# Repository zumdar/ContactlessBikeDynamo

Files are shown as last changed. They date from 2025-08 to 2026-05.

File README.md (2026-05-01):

# Contactless Bicycle Dynamo using Eddy Currents

This is a [certified Open Source](https://certification.oshwa.org/us002771.html) small electrical generator that creates enough current to power a small bicycle light while your wheel is spinning. 

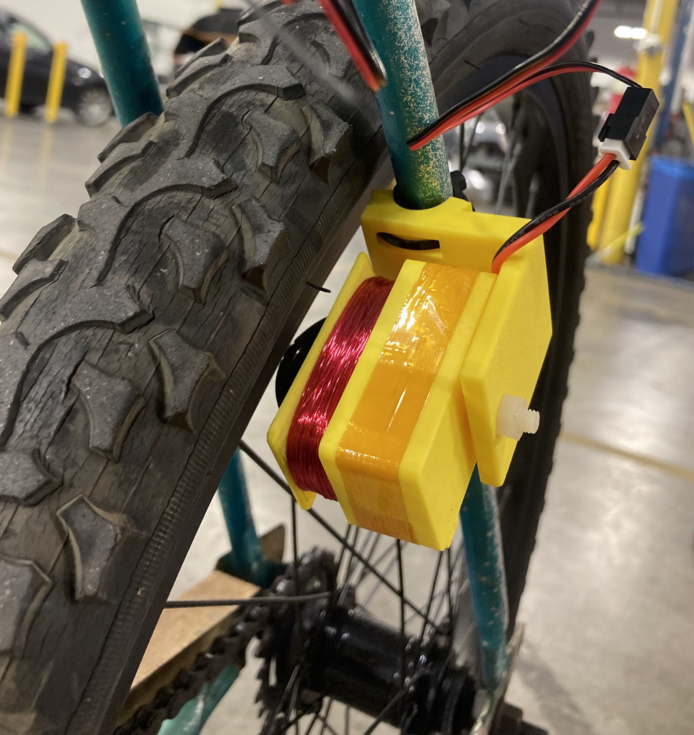
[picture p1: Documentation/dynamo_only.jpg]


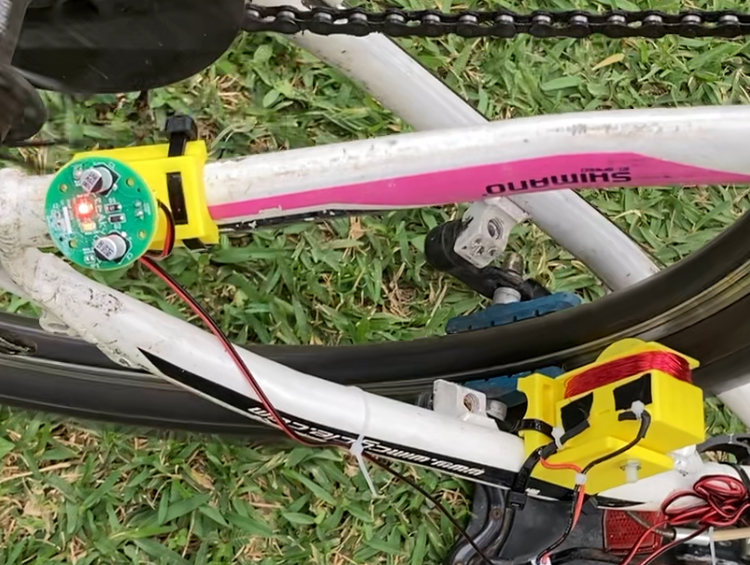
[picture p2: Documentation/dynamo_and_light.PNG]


# Description


The design files here include the physical design files for the Dynamo and the LED light, as well as a custom PCB for the LED light which is a simple voltage rectifier doubler and choice of red or white led. 

If you would like to make this project:
- print off the files in:
  -  \Mechanical\Components\STLs\Final STL
- acquire parts in the Bill of Materials
- aquire tools in the Tool BoM
- follow instructions in the ZINE

This project started off with a desire to be a workshop I could host to show an interesting way to generate electricity and power a bike light without needing a battery. 

Here are the workshop slides:
https://docs.google.com/presentation/d/1txSlyZcSNcTIk4scu_-NPuIz-HN-7od_rSDEqWW2YtM/edit?usp=sharing

# Technical 


## Physical Design Files
The parts are labelled as follows:

- P001-B100	-	Square Dynamo
- P001-B101	-	Dynamo Cover
- P001-B102	-	Magnet Holder Ring
- P001-B103	-	M5 Bearing Adaptor
- P001-B104	-	Fork Bracket
- P001-B105	-	PCB Cover
- P001-B106	-	LED Light Mount

There is also an assembly of the Dynamo labelled:

- P001-B001	-	Dynamo
## PCB Design files

The PCB contains red and white LEDs which can be selected by doing a solder bridge while assembling. 

You can't use both at the same time. If you solder both, only the Red LED will light (it has a lower forward voltage). 

The LED PCB design can be found in:
- \Electrical\Dyno_LED_PCB

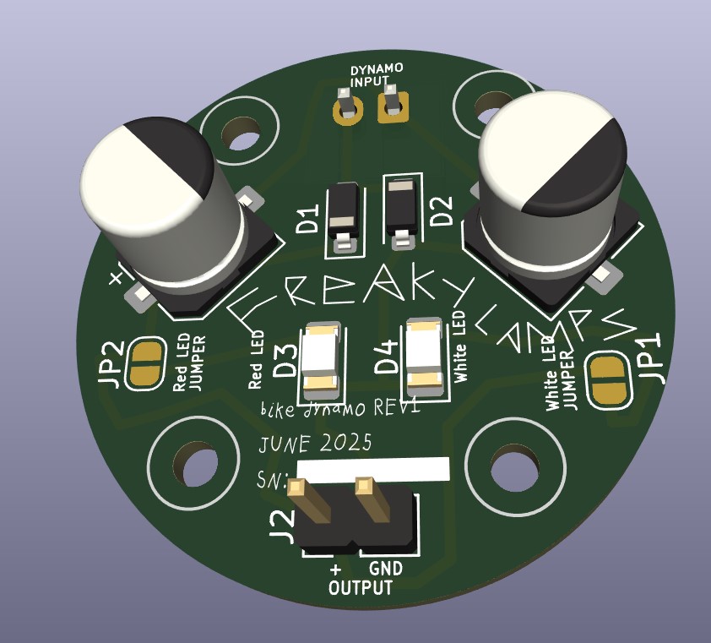
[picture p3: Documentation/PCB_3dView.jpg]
pcb render


# Acknowledgments

Thank you to:
Lucas Ray, Clara Caspard, and YJ Rodrigues for helping develop this! 

# License
This is an certified [open source project](https://certification.oshwa.org/us002771.html)!



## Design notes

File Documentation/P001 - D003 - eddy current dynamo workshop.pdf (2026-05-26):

# free energy

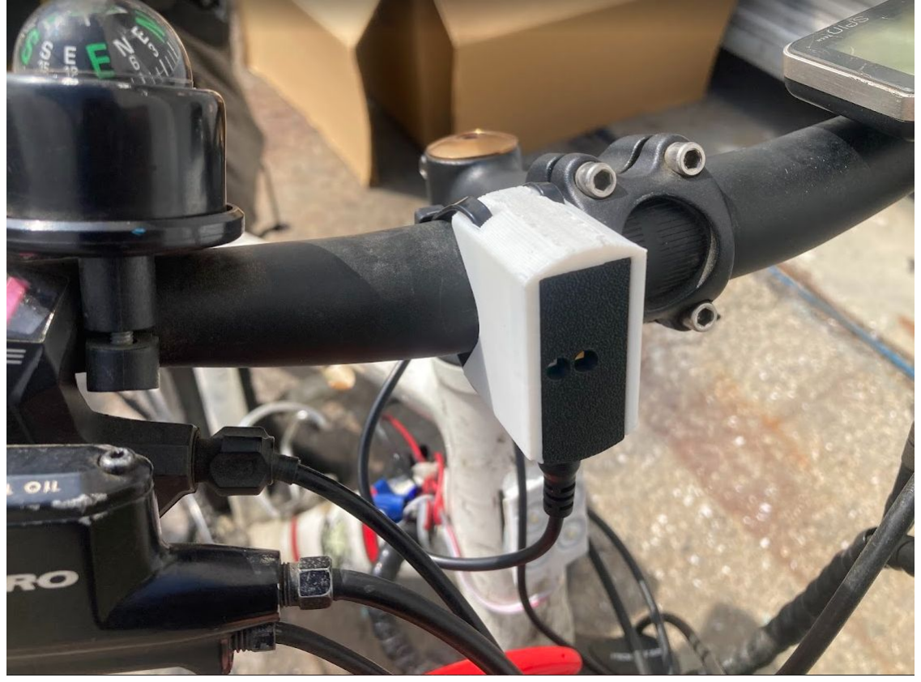
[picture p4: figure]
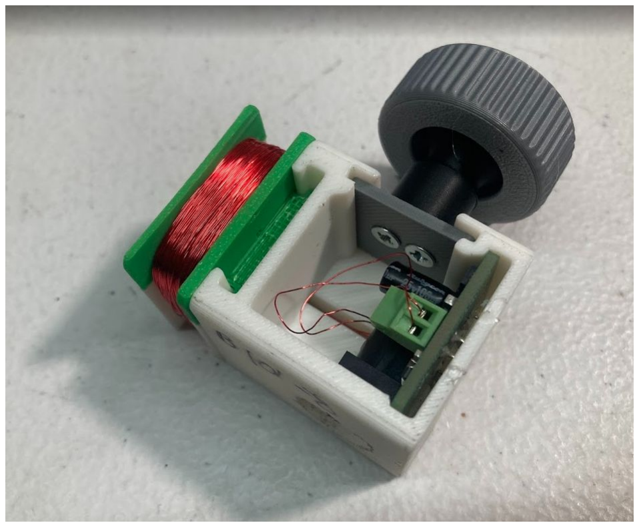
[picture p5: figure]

# contactless bicycle power dynamo (mag’neat’o)

# William Kennedy (freakylamps.com) Open Hardware Summit 2026 Berlin 5.25.2026 https://github.com/zumdar/ContactlessBikeDynamo

# Overview

## - Who am I - Demo - Dynamo tech and history - Eddy Currents and Physics - Make a dynamo - TEST - Hang out

# Bike Demo

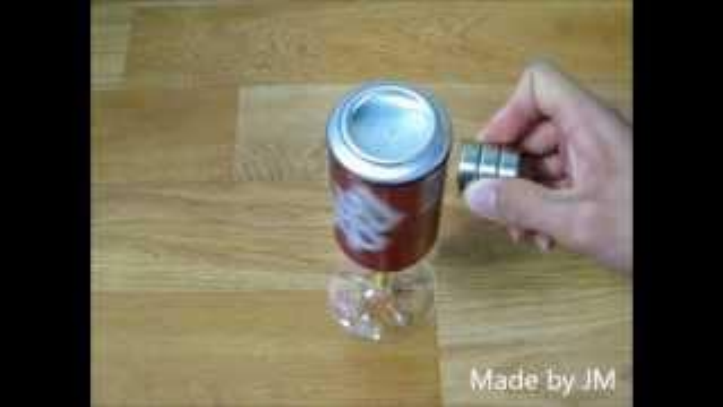
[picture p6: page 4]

# Who am I

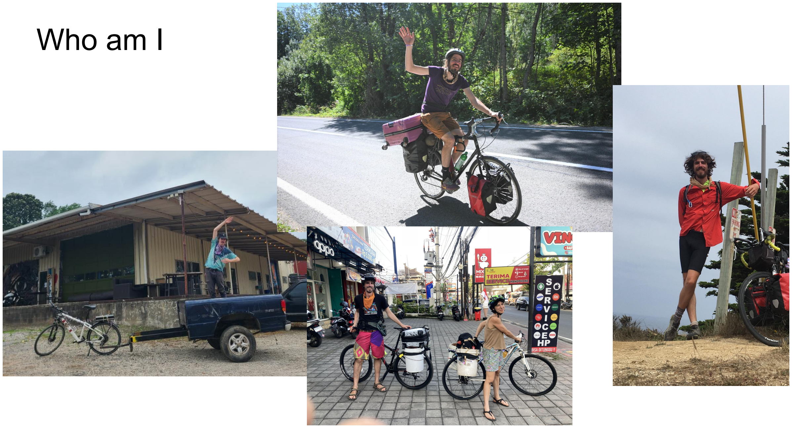
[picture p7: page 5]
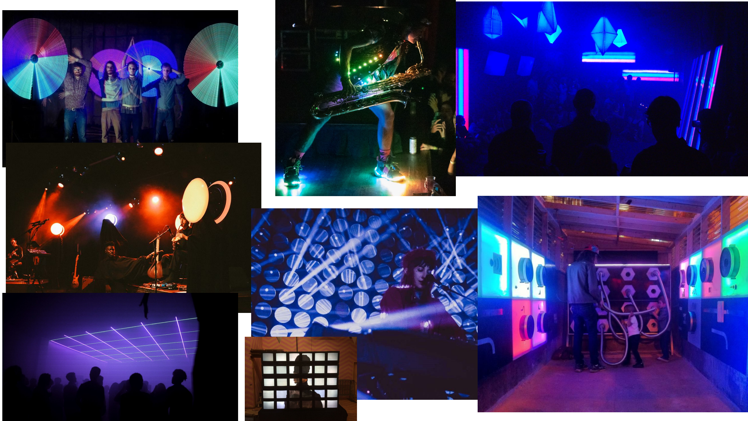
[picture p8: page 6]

# What is a bicycle DYNAMO?

## - small device that converts mechanical energy into electric energy to power

your bike’s lights while you ride.

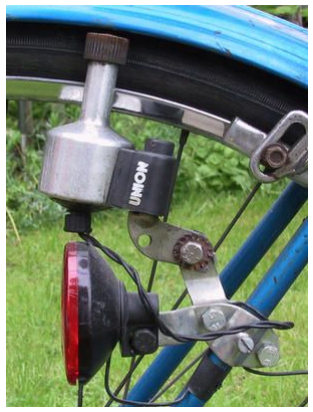
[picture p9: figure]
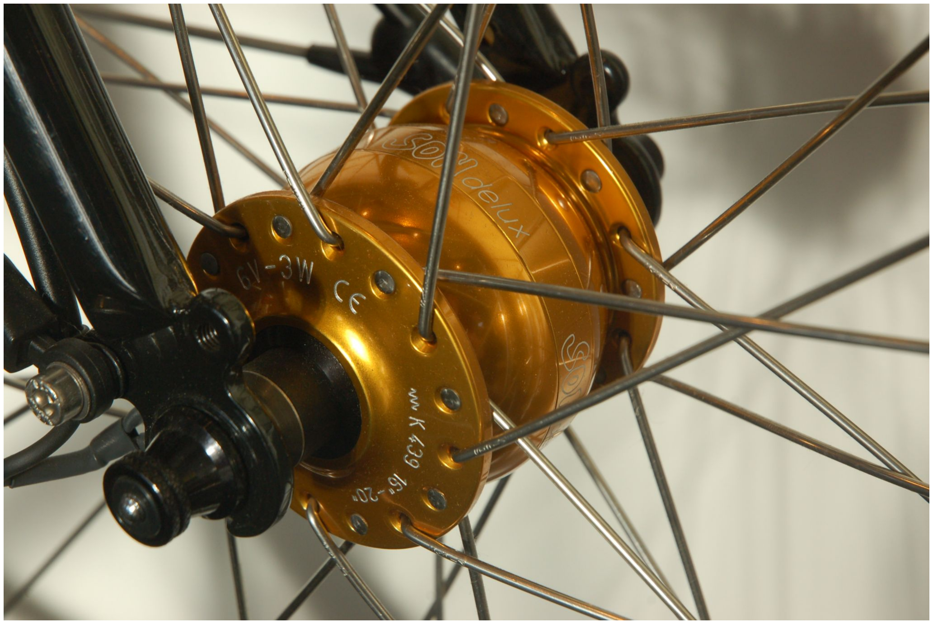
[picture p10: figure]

Hub Dynamo | Bottle Dynamo

# Dynamo? Generator? Magneto? Alternator?

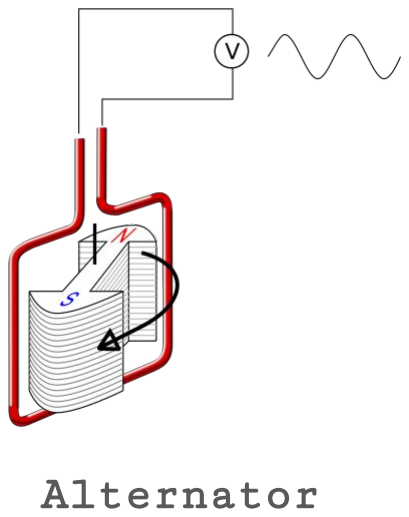
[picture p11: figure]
Alternator

## - Generator

- broad term usually meaning a machine that generates AC

## - Dynamo

- uses an electromagnet and a commutator with spinning wire to create DC

## - Magneto

- uses a permanent magnet and spinning wire to create AC voltage - typically pulsed, not smooth

## - Alternator

- uses a field electromagnet (the rotor) which spins inside of a of stationary coils of wire (the stator) - creates AC

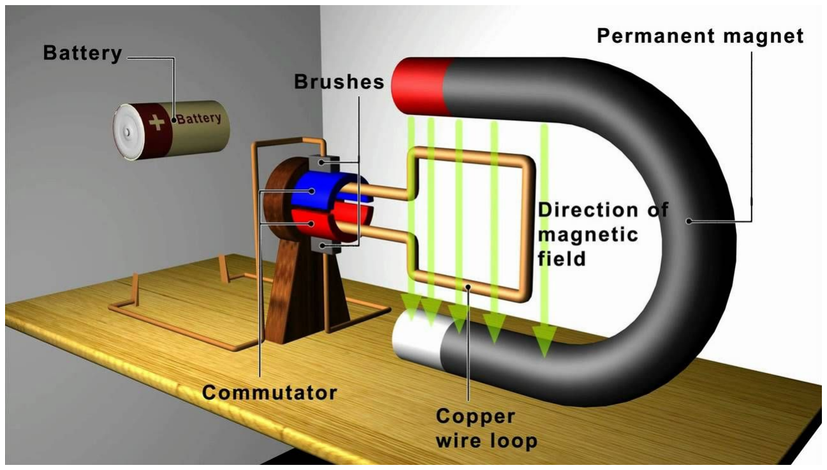
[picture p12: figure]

# Dynamo

# Hub Dynamos

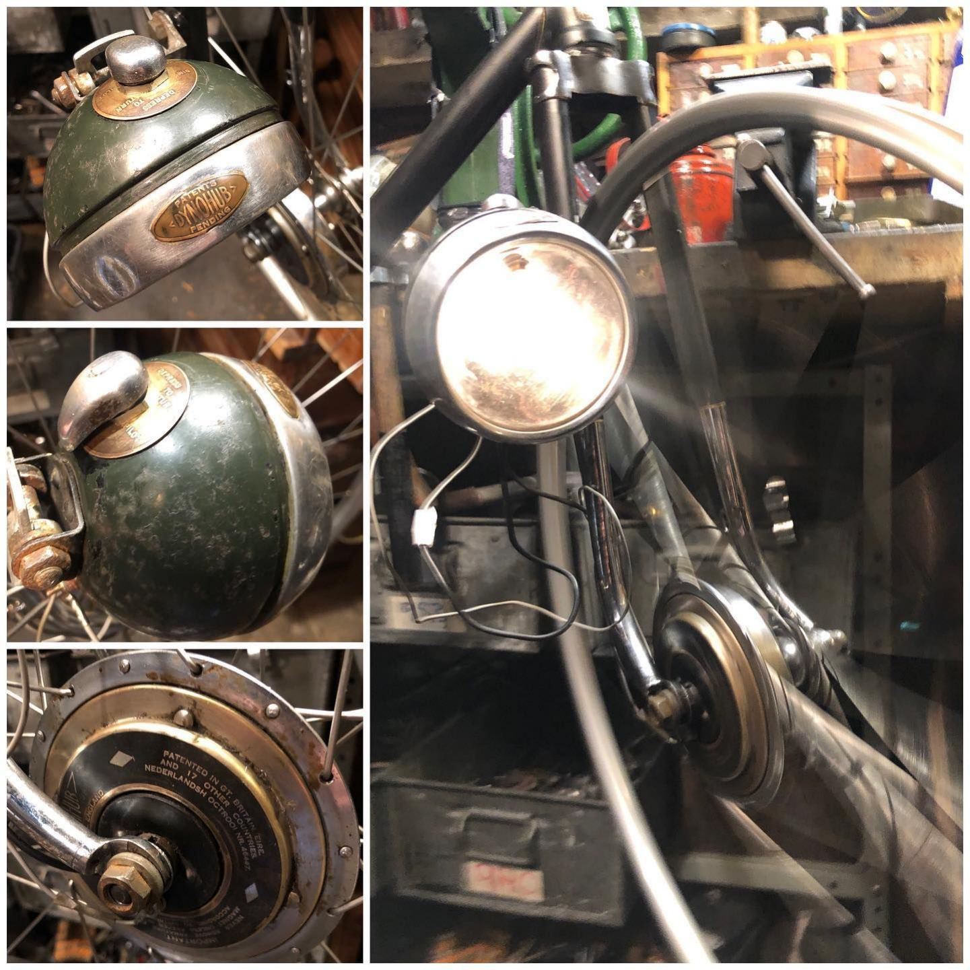
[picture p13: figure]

## - History

- invented in 1936 by Sturmey-Archer in England.
- high drag and low output energy. Declined in 1980s.
- Modern high efficiency dynamo engineered by German engineer Wilfried Schmidt in 1995 (Schmidt Original Nabendynamo (SON))

## - Advantages

- High Efficiency and output (3 watts!)
- very low drag
- reliable
- no adjusting , clean cable wiring, harder to steal

## - Disadvantages

- expensive to purchase and do a wheel build around it
- tied to that one wheel

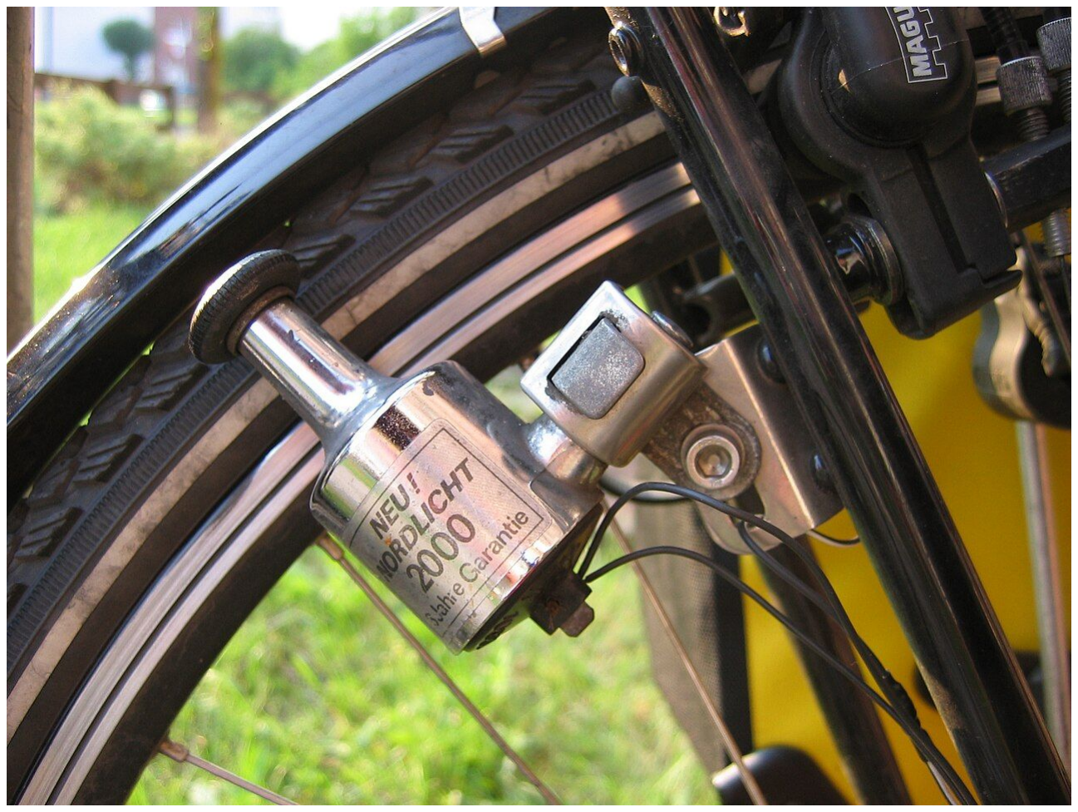
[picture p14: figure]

# Bottle/Sidewall/Rim Dynamo

## - History

### - 1923: German Robert Bosch invented the modern bicycle dynamo - Post WW1 depression - Pre - kerosene lamps, arc lamps with big batteries - 1930s - 1960s golden age for bottle dynamos

## - Advantages

### - Easy to retrofit - lower cost - can be disengaged easily

## - Disadvantages

### - higher drag and friction - more wear and tear (touching wheel) - slippage when wet - can get knocked out of alignment

# Battery Lights

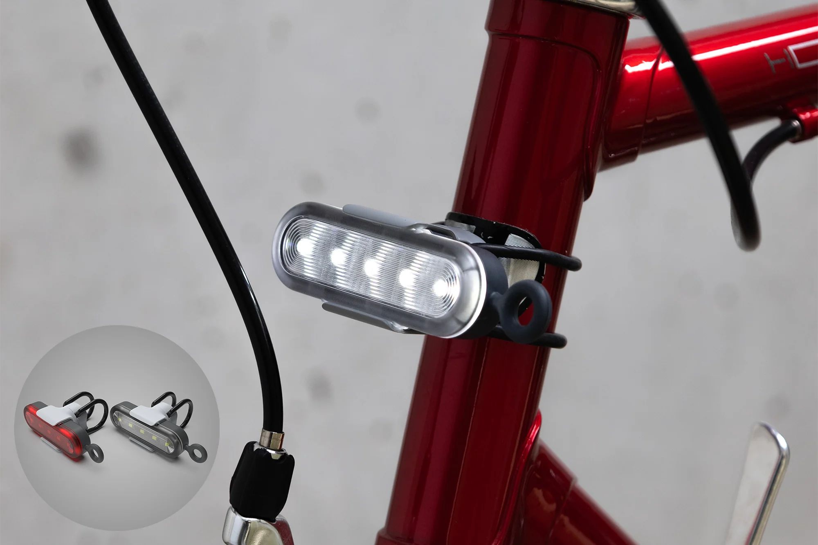
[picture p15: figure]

## - History

- 1896–1900, small torch-style lamps using zinc-carbon dry cells were strapped to handlebars or forks.
- Low self-discharge NiMH battery (LSD-NiMH) in 2005 started allowing better more powerful ights
- Li-ion and LiPo batteries around 2010 supercharged battery powered bike lights

## - Advantage

- High Power
- easy to remove
- rechargeable

## - Disadvantages

- need to recharge
- easily stolen
- charging cables…

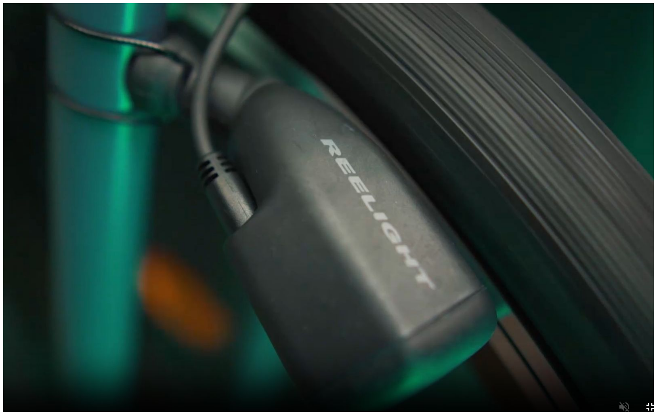
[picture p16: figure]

# Eddy Current Dynamos

## - History

### - Magnic Light (Germany, ~2012) - Reelight - Danish - Wheelswing - South Korea 2017

## - Advantages

### - Zero drag - no friction contact - No tire wear - Works in wet conditions - Easy to install, no wheel rebuild required (unlike hub dynamos) - No batteries to replace - Magic

## - Disadvantages

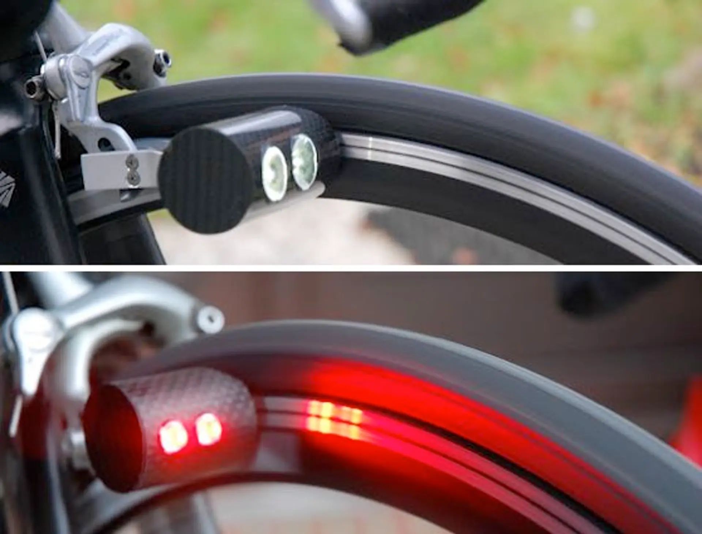
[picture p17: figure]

### - Low power output - need to run cables to light

# Eddy Current Dynamos

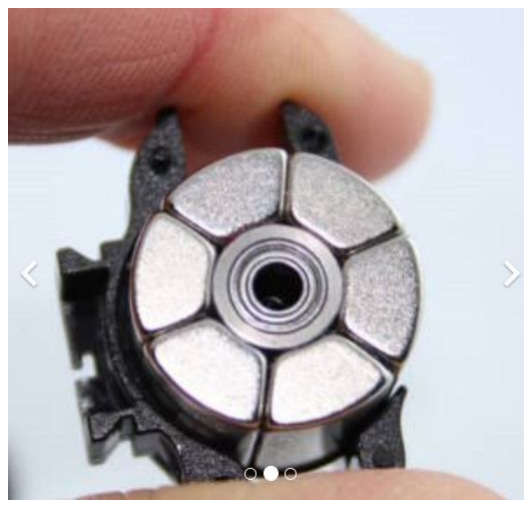
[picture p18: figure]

# EDDY CURRENTS DYNAMOS!

## - Ring of alternating polarity magnets around a bearing

- This ring is placed inside a coil of wire,

## when the magnets are spun, there is an electric current induced in the wire

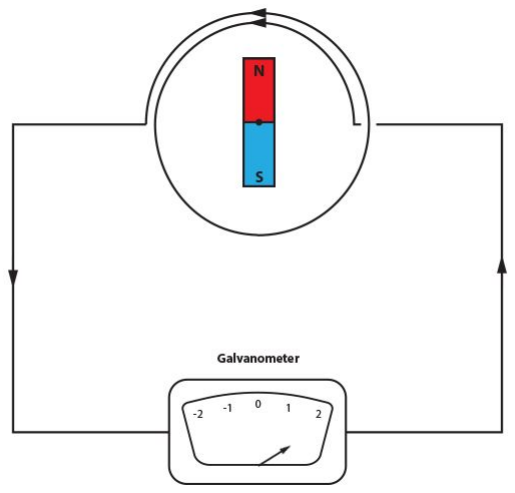
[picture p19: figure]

## - BUT… How does this magnet ring spin?

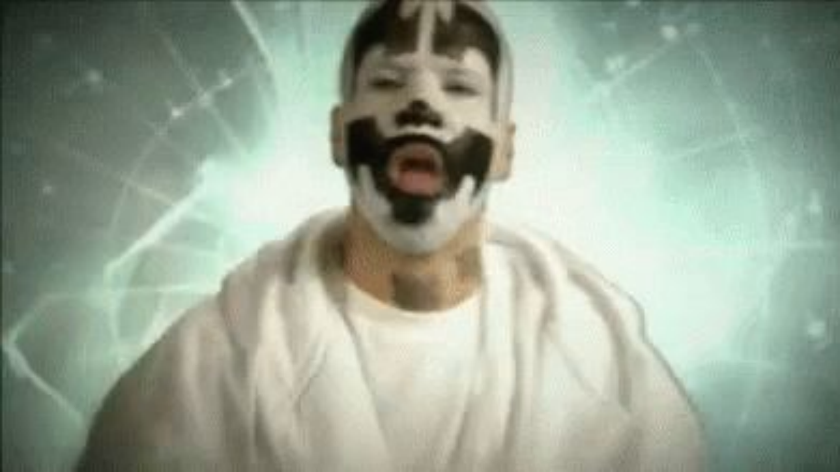
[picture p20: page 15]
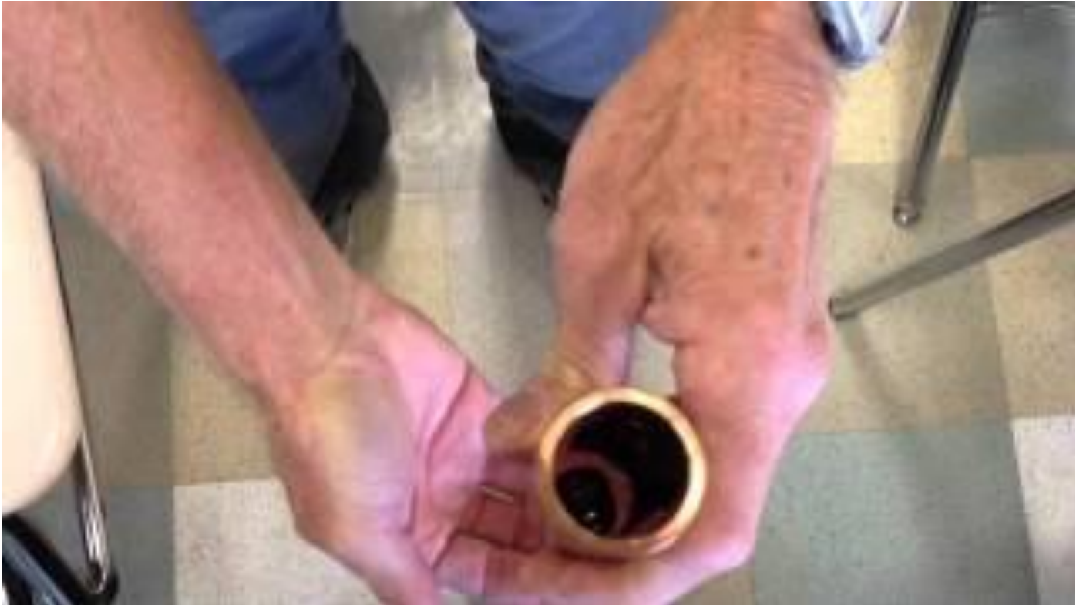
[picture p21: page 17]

# Physics - Electromagnetism

## - Magnetic field

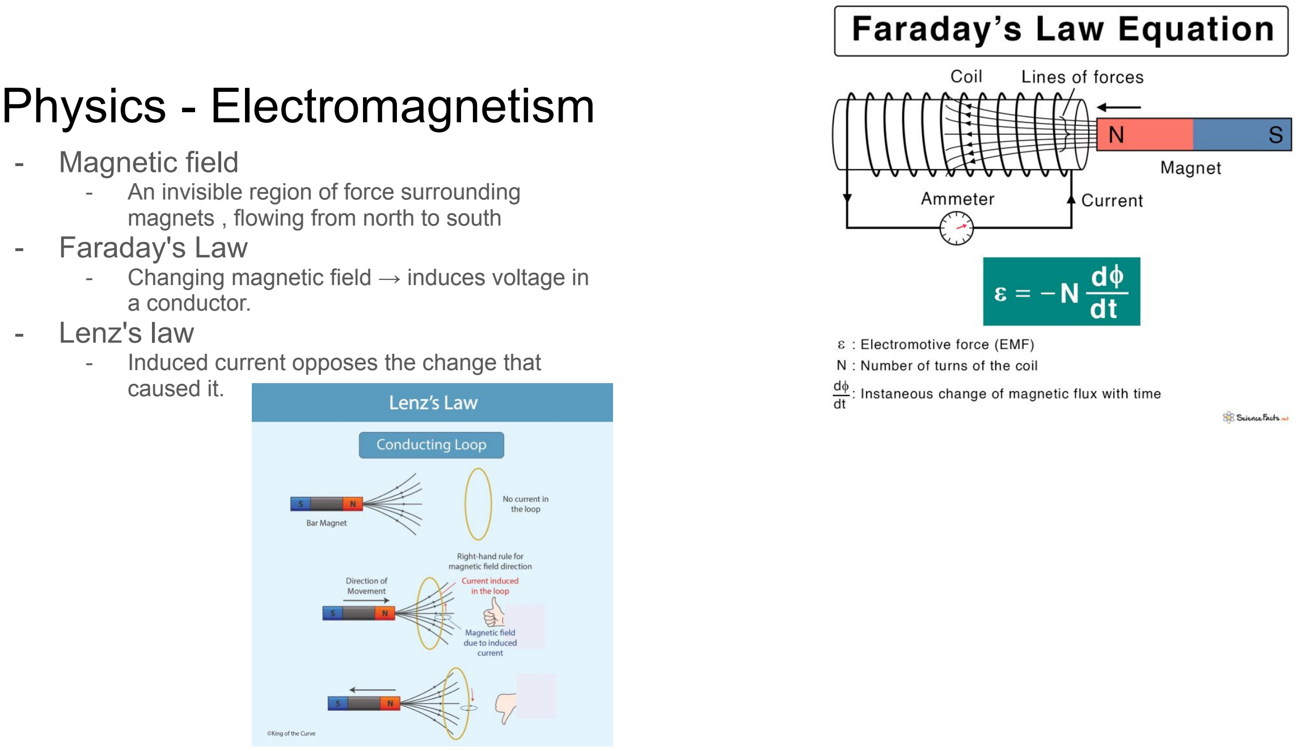
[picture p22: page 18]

- An invisible region of force surrounding magnets , flowing from north to south

## - Faraday's Law

- Changing magnetic field → induces voltage in a conductor.

## - Lenz's law

- Induced current opposes the change that caused it.

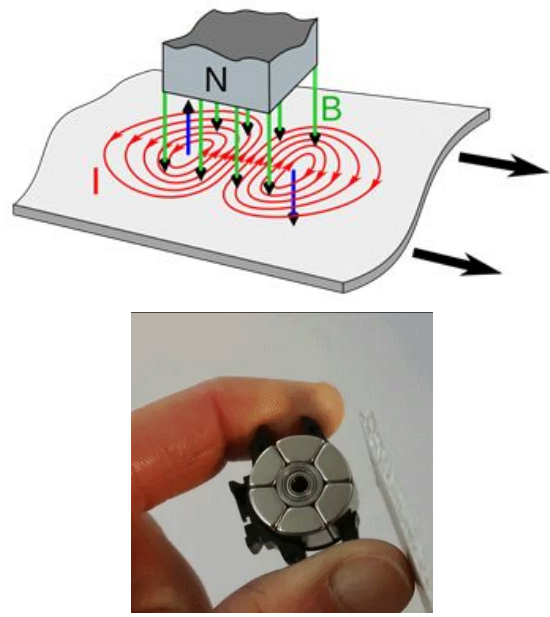
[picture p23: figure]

# Eddy Currents

## - moving magnet near solid conductor - The changing field induces voltage throughout the bulk

metal (Faraday).

## - The resulting currents circulate in loops that resist the magnet's motion (Lenz). Those circulating

loops are eddy currents.

## - Those currents have their own opposing magnetic field (Lenz)

# EDDY CURRENTS DYNAMOS!

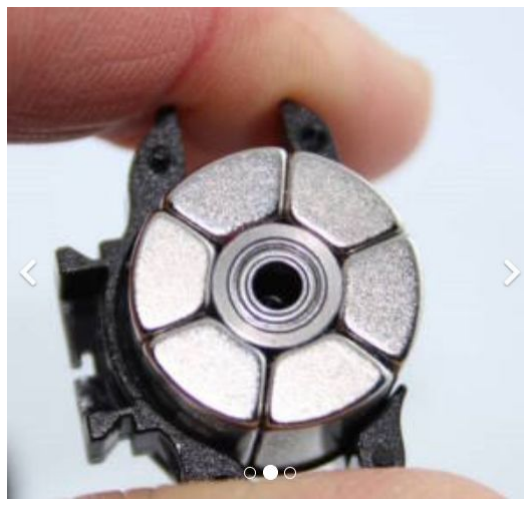
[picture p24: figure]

## - Work by NOT touching the moving bicycle rim - Ring of alternating polarity magnets around a bearing - This is placed near the aluminum rim of bike

- Aluminum is electrically conductive but not magnetic!

## - As the wheel spins, the magnets induce an eddy current in the rim of the wheel - That eddy current has an opposing magnetic field that pushes the magnet ring - The spinning of the magnet ring in a coil of wire induces a current - That current is rectified (AC / DC) and sent to bike light

# The Open Source Eddy Current Dynamo Rev. 2!

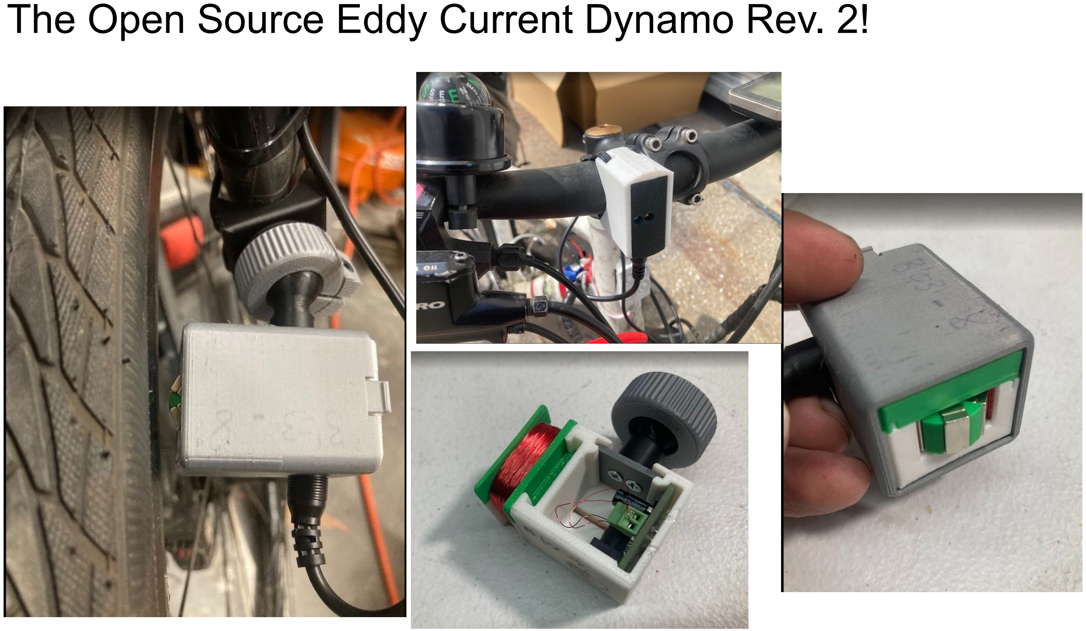
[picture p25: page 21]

# Work to do - Want to get involved?

## - get more power out of it? - circuit to keep light on when you stop pedalling

### - flash or solid

# WORKSHOP THYME

# Special Thanks

## Emma Meyers & Chelsea Dunn - workshop and slide critical feedback

## Kevin Bower - mechanical engineering design help with V2

## Lucas Ray - mechanical engineering design help with V1

## YJ Rodrigues - electrical engineering on V1

## Clara Caspard - mechanical engineering design help with V1

# References

## Patents

- | Non-contact eddy current | generator (https://patents.google.com/patent/KR101540763B1/en?oq=KR101540763B1) - KR101540763B1
- | Eddy Current Generator for Bicycle (https://patents.google.com/patent/US20140070675A1/en?oq=20140070675) | - 20140070675

## Sites referenced:

- DIY Contactless Magnetic Induction Bike Dynamo : 7 Steps - Instructables (https://www.instructables.com/DIY-contactless-magnetic-bike-rim-dynamo/)
- Magnic Light - Eddy Current (https://www.magniclight.com/index.php/en/technology/eddy-current) explanation

## - https://www.sheldonbrown.com/marty_light_hist.html

●

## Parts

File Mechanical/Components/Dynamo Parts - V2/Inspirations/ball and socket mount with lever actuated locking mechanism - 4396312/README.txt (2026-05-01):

ball and socket mount with lever actuated locking mechanism by ply2 on Thingiverse: https://www.thingiverse.com/thing:4396312

Summary:
I use this to temporarily attach my smartphone (as a video camera) to a magnifier desk lamp from ELV.Socket partthe socket part has lego-like bores on the bottom side, arranged in a rectangular 10 x 10 mm grid pattern, the bore diameter in the mesh is 5.6mm, the depth of the pockets is 2 mm, if you create nubs for a counterpart to simplify gluing in place, around 5.0-5.2 mm diam pads with 1.6mm height are recommended for an uncomplicated fit. The socket part has a footprint of 35 x 33 mm.Ball partThe diameter of the stick is 5mm (in the mesh). For good stability it is highy recommended to print it with the stick lying horizontally, no supports are needed (they are baked into the model). Models without supports can be extracted from the attached FreeCad 0.18 project file.LeverTo attach the lever, you can use wire from a paper clip for a regular fit, I ended um using a 2 mm diam steel pin for an extremely tight fit (=strong locking effect on the ball). Please note that, once the wire is glued to the socket part with the lever in place, it is impossible to pull the ball out of the socket without destruction, even when the lock is fully disengaged.PrintingI successfully printed it with a 0.8 mm nozzle, 0.4 mm layer height, 100% infill from PLA. 0.4 mm nozzle i didn't test, i don't see why it (apart from the insane printing time) shouldn't work just as nicely. Please note that you can not print this from PETG, it 's  too slippy, PETG will result in disappointing locking strength.

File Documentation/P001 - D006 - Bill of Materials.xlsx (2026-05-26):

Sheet: V2 Kit BOM
Part Number | Description | Image | Qty | Subsystem
B114 | Bobbin Top |  |  | Bobbin
B100 | Bobbin Bottom |  |  | Bobbin
B102 | Magnet Ring |  |  | Bobbin
B122 | Small Internal Spacer |  |  | Bobbin
B109 | Winding adaptor for drill |  |  | Bobbin
B110 | Enclosure |  |  | Enclosure
B103 | Cover |  |  | Enclosure
B113 | Bike Mount |  |  | Mount
B123 | Rod Shaft |  |  | Mount
B111 | Rod Shaft mounting plate |  |  | Mount
B112 | Nut |  |  | Mount
B124 | Light Enclosure |  |  | Light
B125 | Light Lid |  |  | Light
B115 | Spool Holder |  |  | Optional
B116 | Winder Platform |  |  | Optional
E101 | Rectifier PCB |  |  | Electrical
E102 | LED PCB |  |  | Electrical
 | M3x16 screw |  | 1 | Hardware
 | M3 nut |  | 1 | Hardware
 | #4 x 1/2" wood screw |  | 2 | Hardware
 | M4x40 screw |  | 1 | Hardware
 | M4 nut |  | 1 | Hardware
 | 10x5x2 bar magnets |  | 2 | Bobbin
 | 32 gauge wire |  | 1 oz | Bobbin
 | 8 x 3 x 4 bearing |  | 2 | Bobbin
 | 5mm lens for leds |  | 2 | Light
 | 3 foot male to male barrel cables |  | 1 | Electrical
 | 1.3mm Flat head screwdriver |  | 1 | Tools
 | PH0 Philips head screwderiver |  | 1 | Tools
 | M2.0 Hex key |  | 1 | Tools
 | Drill with adjustable chuck |  | 1 | Tools
 | Knife or wire cutter |  | 1 | Tools
 | 80-220 grit Sandpaper |  |  | Tools
 | Zip ties |  |  | Tools
 | small amount of tape |  |  | Tools
 | CA glue |  |  | Tools
 | bike innertube

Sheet: Mechanical V1
Subsystem | Description | Qty | Footprint Name | Mfg | Mfg Part Number | Reference Designator | Assembly | Notes
Electrical - PCB | White Led | 1 | LED_1206_3216Metric | LCSC | C71796 | D4 | P001-B002 - LED Light
Electrical - PCB | Red LED | 1 | LED_1206_3216Metric | LCSC | C3646938 | D3 | P001-B002 - LED Light
Electrical - PCB | Conn_01x02 | 1 | PinHeader_1x02_P2.54mm_Vertical |  |  | J2 | P001-B002 - LED Light
Electrical - PCB | Conn_01x02 | 1 | JST_XH_B2B-XH-A_1x02_P2.50mm_Vertical | Amazon (https://www.amazon.com/dp/B0D6KSMK1Q?ref_=ppx_hzsearch_conn_dt_b_fed_asin_title_1) |  | J1 | P001-B002 - LED Light
Electrical - PCB | D_Schottky | 2 | D_SOD-123 | LCSC | C8570 | D1, D2 | P001-B002 - LED Light
Electrical - PCB | 100u | 2 | CP_Elec_6.3x7.7 | LCSC | C3338 | C1, C2 | P001-B002 - LED Light
Mechanical - Dynamo | Nylon Slotted Flat Head Screws, M5 x 0.80 mm Thread, 16mm Long | 2 |  | McMaster | 92929A264 |  | P001-B001 - Dynamo | Nylon screw is important because steel will cause magnets not to rotate - CHECK LENGTH
Mechanical - Dynamo | Nylon Hex Nut - M5 x 0.8 mm Thread | 2 |  | McMaster | 93800A550 |  | P001-B001 - Dynamo
Mechanical - Dynamo | 8mm x 3mm Neodymium magnets | 12 |  | Amazon (https://www.amazon.com/dp/B097HCT436) |  |  | P001-B001 - Dynamo
Mechanical - Dynamo | Enamelled Copper Wire | 2.5oz - 3oz |  | Amazon (https://www.amazon.com/dp/B0CJTBQDGK?ref_=ppx_hzsearch_conn_dt_b_fed_asin_title_1&th=1) |  |  | P001-B001 - Dynamo
Mechanical - Dynamo | Tape (electrical or kapton) | 4" |  |  |  |  | P001-B001 - Dynamo
Mechanical - Dynamo | JST-XH 2.54mm Pitch 2 Pin | 1 |  | Amazon (https://www.amazon.com/dp/B0D6KSMK1Q?ref_=ppx_hzsearch_conn_dt_b_fed_asin_title_1) |  |  | P001-B001 - Dynamo
Mechanical - Dynamo | Small zip ties (4" length - 0.1" width) | 2 |  | Amazon (https://www.amazon.com/dp/B0BC1VH4XB?ref_=ppx_hzsearch_conn_dt_b_fed_asin_title_1&th=1) |  |  | P001-B001 - Dynamo
Mechanical - Dynamo | 1/8" shrink tubing | 6" |  | Amazon (https://www.amazon.com/Inch-XHF-Waterproof-Insulation-Wear-Resistant/dp/B0919GN3SX) |  |  | P001-B001 - Dynamo
Mechanical - Dynamo | 10mm diameter lens | 1 |  | Amazon (https://www.amazon.com/dp/B0DRK34V83?ref_=ppx_hzsearch_conn_dt_b_fed_asin_title_1) |  |  | P001-B001 - Dynamo
Mechanical - Dynamo | Passivated 18-8 Stainless Steel Pan Head Phillips Screws - M2 x 0.4mm Thread, 10mm Long | 2 |  | McMaster | 92000A017 |  | P001-B001 - Dynamo | CHECK LENGTH
Mechanical - Dynamo | JST XH Extension cable | 1 |  | Amazon (https://www.amazon.com/dp/B09BN5X6ZT) |  |  | P001-B001 - Dynamo
Mechanical - Dynamo | Larger zip ties (12" length - 0.19" width) | 4 |  | Amazon (https://www.amazon.com/dp/B0BRXZ9RQG) |  |  | P001-B001 - Dynamo

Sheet: kit bom for print
Part Number | Description | Image | Qty | Part Number | Description | Image | Qty
B114 | Bobbin Top |  |  | B112 | Nut
B100 | Bobbin Bottom |  |  | B124 | Light Enclosure
B102 | Magnet Ring |  |  | B125 | Light Lid
B122 | Small Internal Spacer |  |  | B115 | Spool Holder
B109 | Winding adaptor for drill |  |  | B116 | Winder Platform
B110 | Enclosure |  |  | E101 | Rectifier PCB
B103 | Cover |  |  | E102 | LED PCB
B113 | Bike Mount |  |  |  | M3x16 screw |  | 1
B123 | Rod Shaft |  |  |  | M3 nut |  | 1
B111 | Rod Shaft mounting plate |  |  |  | #4 x 1/2" wood screw |  | 2
 | M4x40 screw |  | 1 | 1.3mm Flat head screwdriver |  |  | 1
 | M4 nut |  | 1 | PH0 Philips head screwderiver |  |  | 1
 | 10x5x2 bar magnets |  | 2 | M2.0 Hex key |  |  | 1
 | 32 gauge wire |  | 1 oz | Drill with adjustable chuck |  |  | 1
 | 8 x 3 x 4 bearing |  | 2 | Knife or wire cutter |  |  | 1
 | 5mm lens for leds |  | 2 | 80-220 grit Sandpaper
 | 3 foot male to male barrel cables |  | 1 | Zip ties
 |  |  |  | small amount of tape
 |  |  |  | CA glue
 |  |  |  | bike innertube

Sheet: Rev2 BOM
item | Purpose | unit | price | units per assmebly | price per unit | price per assembly | link | include? | price per one assembly | $6.18
8 x 3 x 4 bearing |  | 30 | $7.99 | 2 | $0.27 | $0.53 | amazon (https://www.amazon.com/dp/B0DHCLF9S3?ref=ppx_yo2ov_dt_b_fed_asin_title&th=1) | TRUE | price for 20 sets | $123.53
32 gauge wire |  | 2 oz | $8.79 | 2 oz |  | $8.79 |  | FALSE
32 gauge wire |  | 4 oz | $12.98 | 1 |  | $3.25 | amazon (https://www.amazon.com/dp/B07JBQQR38?ref=ppx_yo2ov_dt_b_fed_asin_title) | TRUE
10x5x2 bar magnets |  | 120 | $23.99 | 12 | $0.20 | $2.40 |  | TRUE
3 foot male to male barrel cables |  | 5 | $14.50 | 1 | $0.12 | $2.90 |  | FALSE
5mm lens for leds |  | 2 |  |  | $0.00 | $0.00 |  | FALSE
m3 screw for locking nut | locking nut | 1 |  |  |  |  |  | FALSE
m3 nut for locking nut |  | 1 |  |  |  |  |  | FALSE
m4 screw for winding | keeping the bobbin on the winding | 1
m4 nut |  | 1
#4 sheet metal screw | for attaching plate to ball rod | 2
empty spool

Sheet: K and J Magnet Comparisons
name | SKU | price per unit (>100) | magnetization | Diamter (mm) | thickness (mm) | surface field *gauss | grade | pull force 1 lbs
1/4 x 1/8 Inch Neodymium Rare Earth Diametric Disc Magnet N52 | D42DIA-N52 | $0.58 | Diametrically | 6.35 | 3.17 | 7734
5/16 x 1/4 Inch Neodymium Rare Earth Disc Magnet N52 (https://www.kjmagnetics.com/d54-n52-neodymium-disc-magnet) | D54-N52 | $1.10 | Axially | 7.94 | 6.35 | 6275 | N52 | 6.32
5/16 x 1/8 Inch Neodymium Rare Earth Disc Magnet N52 (https://www.kjmagnetics.com/d52-n52-neodymium-disc-magnet) | D52-N52 | $0.66 | Axially | 7.94 | 3.17 | 4623 | N52 | 4.15
5/16 x 5/16 Inch Neodymium Rare Earth Cylinder/Rod Magnet N52 (https://www.kjmagnetics.com/d55-n52-neodymium-cylinder-magnet) | D55-N52 | $1.30 | Axially | 7.94 | 7.94 | 6619 | N52 | 6.73
5/16 x 5/16 Inch Neodymium Rare Earth Cylinder/Rod Magnet N42 (https://www.kjmagnetics.com/d55-neodymium-cylinder-magnet) | D55 | $1.07 | Axially | 7.94 | 7.94 | 5903 | N42 | 6.49
1/4 x 1/8 Inch Neodymium Rare Earth Surplus Disc Magnet N48 (https://www.kjmagnetics.com/zd42-neodymium-disc-magnet) | ZD42 | $0.38 | Axially | 6.35 | 3.17 | 5020 | N42 | 2.63
1/4 x 1/8 Inch Neodymium Rare Earth Disc Magnet N52 (https://www.kjmagnetics.com/d42b-n52-neodymium-disc-magnet) | D42B-N52 | $0.49 | Axially | 6.35 | 3.17 | 5233 | N52 | 2.85

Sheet: Tools Needed
Tool | Size | Qty
Wire Stripper | AWG 30 - | 1
Flat head screwdriver | small | 1
Magnetic Polarity Tester |  | 1 | optional
Drill with adjustable chuck |  | 1
Knife |  | 1
Sandpaper | 80 - 220 grit | small piece
Soldering Iron |  | 1
Solder |  | 1'
CA Glue

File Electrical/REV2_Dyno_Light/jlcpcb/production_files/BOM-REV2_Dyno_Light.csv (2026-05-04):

Comment | Designator | Footprint | LCSC | Quantity
Barrel_Jack_MountingPin | J2 | BarrelJack_Horizontal | C16214 | 1
White 150mA | D2 | LED_PLCC_2835 | C210320 | 1
White 60mA | D1 | LED_PLCC_2835 | C210310 | 1
Red LED | D3 | LED_PLCC_2835 |  | 1

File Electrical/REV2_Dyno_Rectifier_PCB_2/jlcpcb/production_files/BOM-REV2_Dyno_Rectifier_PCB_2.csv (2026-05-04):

Comment | Designator | Footprint | LCSC | Quantity
1.5uH | L1 | L_1008_2520Metric | C5339200 | 1
1.8 | R5 | R_0402_1005Metric | C2960794 | 1
100k | R4 | R_0402_1005Metric | C25741 | 1
100nF | C4 | C_0603_1608Metric | C14663 | 1
100u | C1 | CP_Radial_D5.0mm_P2.00mm | C108360 | 1
10k | R1 | R_0402_1005Metric | C25744 | 1
10uF | C10,C2,C8,C9 | C_0805_2012Metric | C440198 | 4
10uF | C3,C5 | C_0603_1608Metric | C96446 | 2
150k | R3 | R_0402_1005Metric | C2909320 | 1
2.2uH | L2 | L_1008_2520Metric | C394950 | 1
360k | R2 | R_0402_1005Metric | C2909351 | 1
47uF | C6 | C_0805_2012Metric | C16780 | 1
Barrel_Jack_MountingPin | J2 | BarrelJack_Horizontal | C16214 | 1
D_Schottky | D1,D2,D3,D4,D5 | D_SOD-923 | C2886012 | 5
Dynamo Input | J1 | TerminalBlock_Xinya_XY308-2.54-2P_1x02_P2.54mm_Horizontal | C557685 | 1
PAM2803AAF095 | U2 | PAM2803_SOT-23-6_L2.9-W1.6-P0.95-LS2.8-BR | C55801 | 1
TPS63070RNMR | U1 | TPS63070RNMR-2 | C109322 | 1
1F - 2.7V | C7 | supercapacitor - 4mm diameter |  | 1

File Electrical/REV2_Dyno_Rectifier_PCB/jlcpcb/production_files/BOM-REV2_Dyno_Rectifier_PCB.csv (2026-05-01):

Comment | Designator | Footprint | LCSC | Quantity
100u | C1,C2 | CP_Elec_6.3x7.7 | C3338 | 2
Barrel_Jack_MountingPin | J3 | BarrelJack_Horizontal | C16214 | 1
D_Schottky | D1,D2 | D_SOD-123 | C8570 | 2
Screw_Terminal_01x02 | J2 | TerminalBlock_Xinya_XY308-2.54-2P_1x02_P2.54mm_Horizontal | C557685 | 1

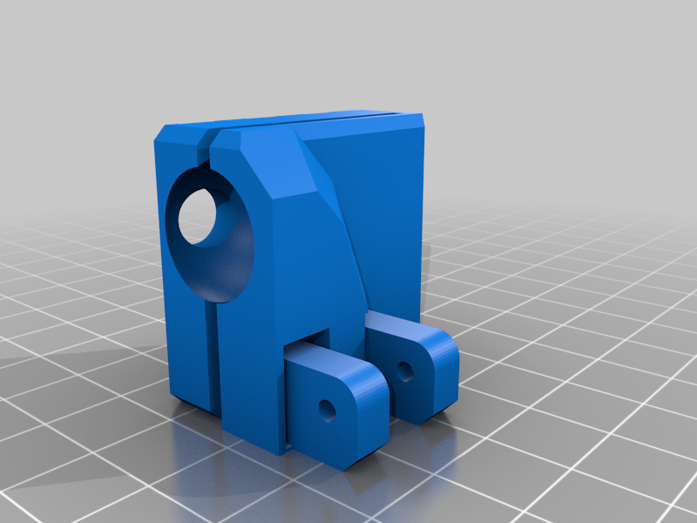
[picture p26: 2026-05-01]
Mechanical/Components/Dynamo Parts - V2/Inspirations/ball and socket mount with lever actuated locking mechanism - 4396312/images/out_Socket_Meshed.png

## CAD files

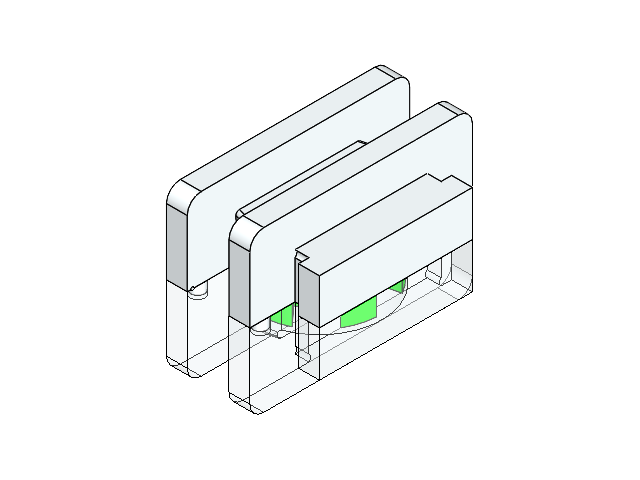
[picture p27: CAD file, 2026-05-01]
Mechanical/Components/Dynamo Parts - V2/Dynamo Assembly_2D-1/Dynamo Assembly_2D-1.SLDASM
P001-B100_SquareDynamo_Rev2D-1 x 2
Magnet Ring

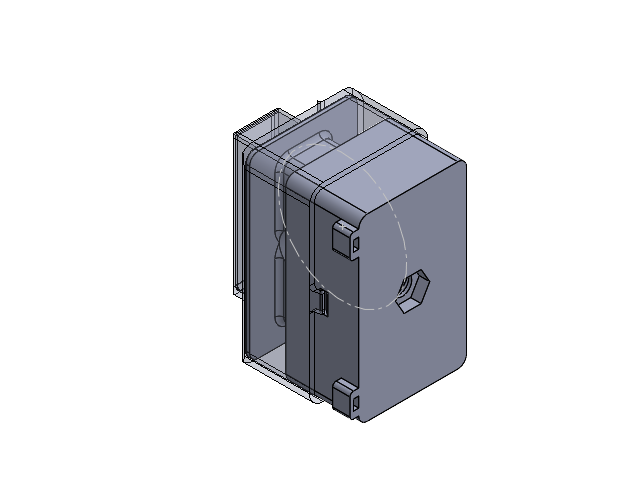
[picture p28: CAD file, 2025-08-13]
Mechanical/Components/P001-B001K_Dynamo.SLDASM
P001-B102P_MagnetHolderRing
5972K222_Ball Bearing
P001-B100P_SquareDynamo
P001-B101E_DynamoCover

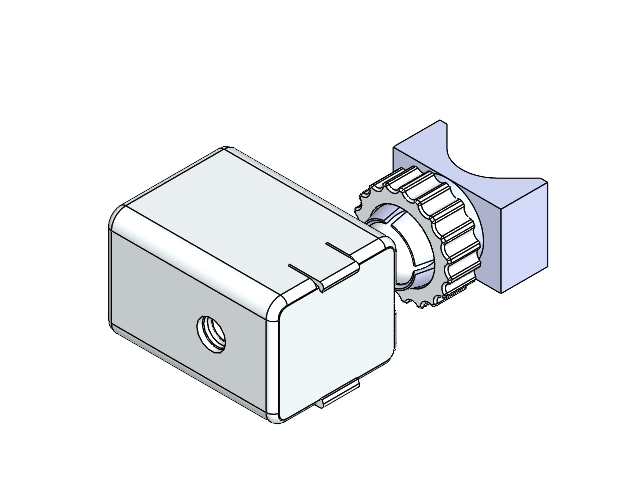
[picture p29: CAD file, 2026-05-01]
Mechanical/Components/Dynamo Parts - V2/Dynamo Assembly_Rev2D/Dynamo Assembly_Rev2D/Dynamo Assembly_2D-1.SLDASM
P001-B100_SquareDynamo_Rev2D-3 x 2
Magnet Ring
P001-B101_RearEnclosure_Rev2D-1
DC Power Jack 5.5mm x 2.1mm
9262K142_Oil-Resistant Buna-N O-Ring
P001-B102_BallMount_Rev2D-1
P001-B105_BikeMount_Rev2D-1
P001-B103_FrontCover_Rev2D-1
P001-B104_BallNut_Rev2D-1

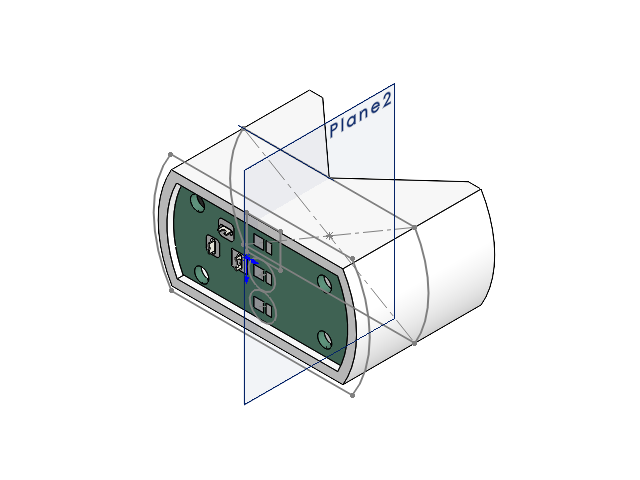
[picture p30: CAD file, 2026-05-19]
Mechanical/Components/Dynamo Parts - V2/P001-B007_REV2 Light.SLDASM
BarrelJack_Horizontal_2.step
REV2_Dyno_Light_pad_1.step
REV2_Dyno_Light_PCB_1.step
P001-B124_REV2 Light Cover
Part24^P001-B007_REV2 Light

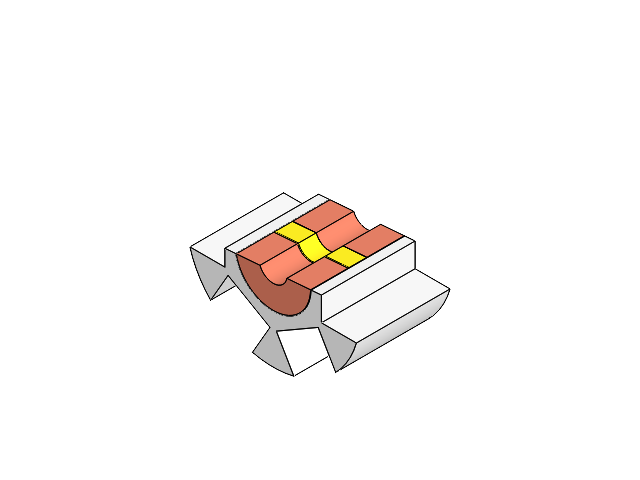
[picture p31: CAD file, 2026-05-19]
Mechanical/Components/Dynamo Parts - V2/P001-B005-Magnet Ring Assembly.SLDASM
P001-B102_MagnetHolderRing_Rev2C_7
8x3x4 Ball Bearing x 2
P001-B122-Magnet Ring Bearing Adaptor_3

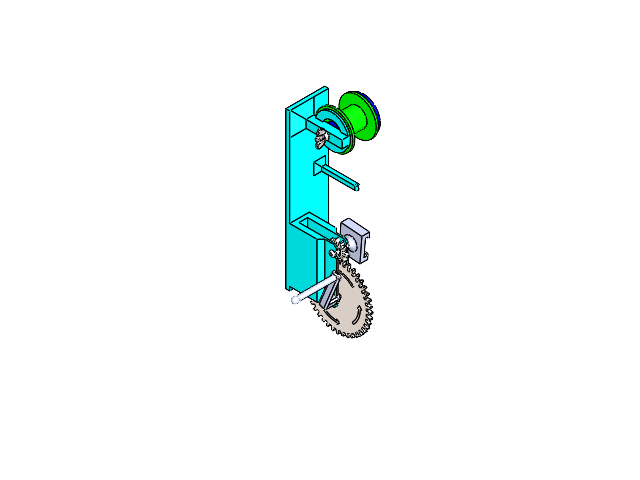
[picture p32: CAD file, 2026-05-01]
Mechanical/Components/Dynamo Parts - V2/SpoolingAssembly/P001-B003_SpoolingAssembly.SLDASM
P001-B116_WinderPlatform-1
Spool
P001-B118_SpoolWasher-1
92000A343_Passivated 18-8 Stainless Steel Pan Head Phillips Screws
94300A320_Zinc-Plated Steel Wing Nut
大齿轮
小齿轮
P001-B120_LargeGearShaft
P001-B121_CrankHandle-1
P001-B119_BobbinDriveShaft-1

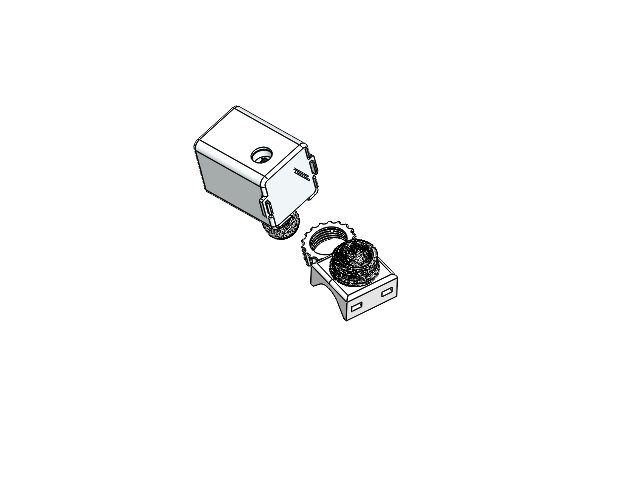
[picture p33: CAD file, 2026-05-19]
Mechanical/Components/Dynamo Parts - V2/P001_B110_Dynamo Assembly_2D-2.SLDASM
Magnet Ring
P001-B101_RearEnclosure_Rev2D-10
P001-B123_Mount_Rod_5
P001-B105_BikeMount_Rev2D-6
P001-B103_FrontCover_Rev2D-9
P001-B104_BallNut_Rev2D-1
P001-B100_SquareDynamo_Rev2D-14
P001-B114_SquareDynamoTop_8
DG308-2.54-pin-0.step x 2
DG308-2.54-contact.step x 2
DG308-2.54-screw.step x 2
DG308-2.54-02P-1.step
L_1008_2520Metric.step x 2
C_0603_1608Metric.step x 3
R_0402_1005Metric.step x 5
BarrelJack_Horizontal.step
D_SOD-923.step x 5
C_0805_2012Metric.step x 5
CP_Radial_D5.0mm_P2.00mm.step
supercap_1f_CXHP2R7105R-TWX.step
REV2_Dyno_Rectifier_PCB_2_PCB.step
P001-B111_BallMount_4

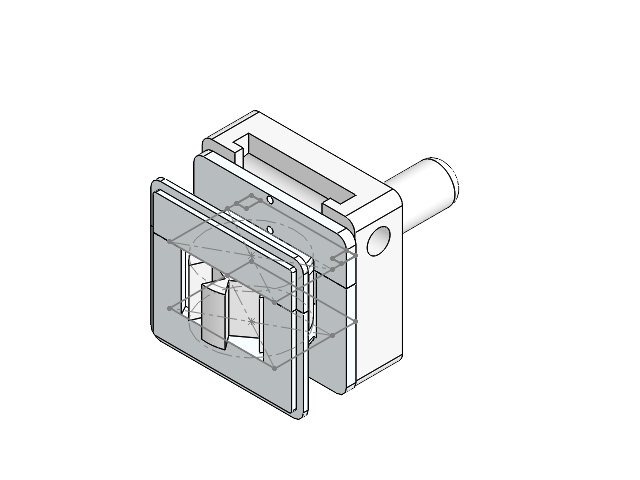
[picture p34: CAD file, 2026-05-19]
Mechanical/Components/Dynamo Parts - V2/P001-B008_Bobbin_DrillWindingAttachment.SLDASM
P001-B109_Winding_Plate_Attachment_5
P001-B114_SquareDynamoTop_7
P001-B100_SquareDynamo_Rev2D-13
P001-B102_MagnetHolderRing_Rev2C_7

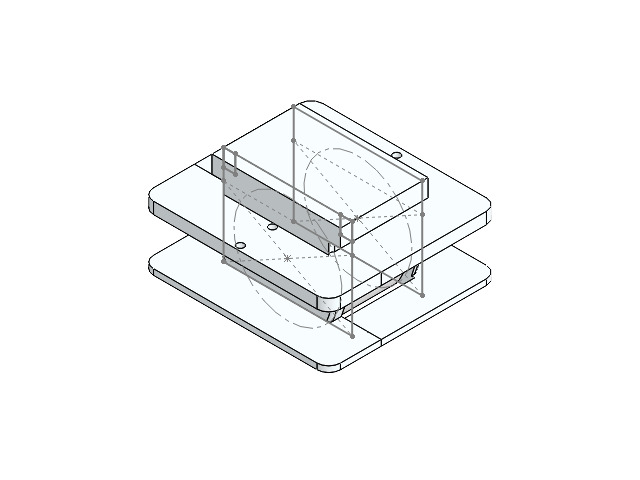
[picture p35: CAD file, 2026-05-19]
Mechanical/Components/Dynamo Parts - V2/P001_B004_Bobbin_1.SLDASM
P001-B114_SquareDynamoTop_7
P001-B100_SquareDynamo_Rev2D-13
P001-B102_MagnetHolderRing_Rev2C_7

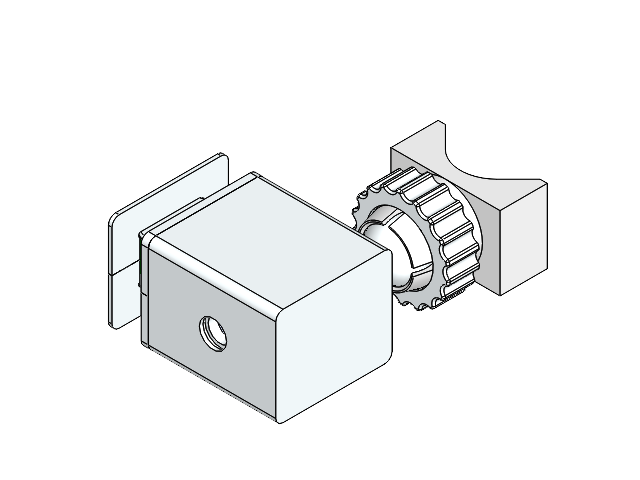
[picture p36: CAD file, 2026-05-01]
Mechanical/Components/Dynamo Parts - V2/Dynamo Assembly_2D-1.SLDASM
P001-B100_SquareDynamo_Rev2D-3 x 2
Magnet Ring
P001-B101_RearEnclosure_Rev2D-1
P001-B102_BallMount_Rev2D-1
P001-B105_BikeMount_Rev2D-1
P001-B104_BallNut_Rev2D-1
DG308-2.54-pin-0_3.step x 2
DG308-2.54-contact_3.step x 2
DG308-2.54-screw_3.step x 2
DG308-2.54-02P-1_3.step
L_0603_1608Metric.step x 2
C_0603_1608Metric.step x 3
R_0402_1005Metric.step x 5
BarrelJack_Horizontal_3.step
D_SOD-923.step x 5
C_0805_2012Metric.step x 4
CP_Radial_D5.0mm_P2.00mm.step
supercap_1f_CXHP2R7105R-TWV.step
REV2_Dyno_Rectifier_PCB_2_PCB.step

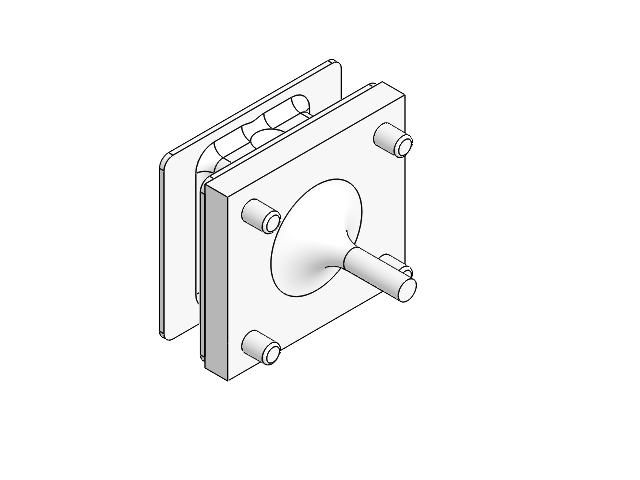
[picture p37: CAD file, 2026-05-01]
Mechanical/Components/Dynamo Parts - V2/Dynamo_Rev2C_2.SLDASM
P001-B100_SquareDynamo_Rev2C_3
P001-B109_WindingPlateAttachment
P001-B102_MagnetHolderRing_Rev2C_3

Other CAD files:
Electrical/REV2_Dyno_Rectifier_PCB/REV2_Dyno_Rectifier_PCB2.SLDASM
Mechanical/Components/Dynamo Parts - V2/P001-B007_REV2 Light_2.SLDASM
Electrical/REV2_Dyno_Rectifier_PCB_2/REV2_Dyno_Rectifier_PCB3.SLDASM
Electrical/REV2_Dyno_Rectifier_PCB/REV2_Dyno_Rectifier_PCB3.SLDASM
Mechanical/Components/Dynamo Parts - V2/P001-B006_RearEnclosurewithPCB.SLDASM
Mechanical/Components/Dynamo Parts - V2/P001-B007_REV2 Light_4.SLDASM
Mechanical/Components/Dynamo Parts - V2/P001-B007_REV2 Light_3.SLDASM
Documentation/bike Dynamo.blend
Electrical/Dyno_LED_PCB/Dyno_LED_PCB.step
Electrical/REV2_Dyno_Rectifier_PCB/REV2_Dyno_Rectifier_PCB.SLDASM
Electrical/REV2_Dyno_Rectifier_PCB/REV2_Dyno_Rectifier_PCB.step
Electrical/REV2_Dyno_Rectifier_PCB_2/REV2_Dyno_Rectifier_PCB2.SLDASM
Electrical/REV2_Dyno_Rectifier_PCB_2/REV2_Dyno_Rectifier_PCB_2.SLDASM
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

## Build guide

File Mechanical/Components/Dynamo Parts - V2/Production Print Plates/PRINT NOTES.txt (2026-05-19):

B105 - Bike mount - 
- Make sure you stand it up, cant have supports inside the zip tie cavity
- Need Thin Wall Support on 
Dynamo Top
- using 0.12mm layers

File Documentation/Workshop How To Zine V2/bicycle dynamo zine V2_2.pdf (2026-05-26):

# put bearing+ring+ bearing sandwich

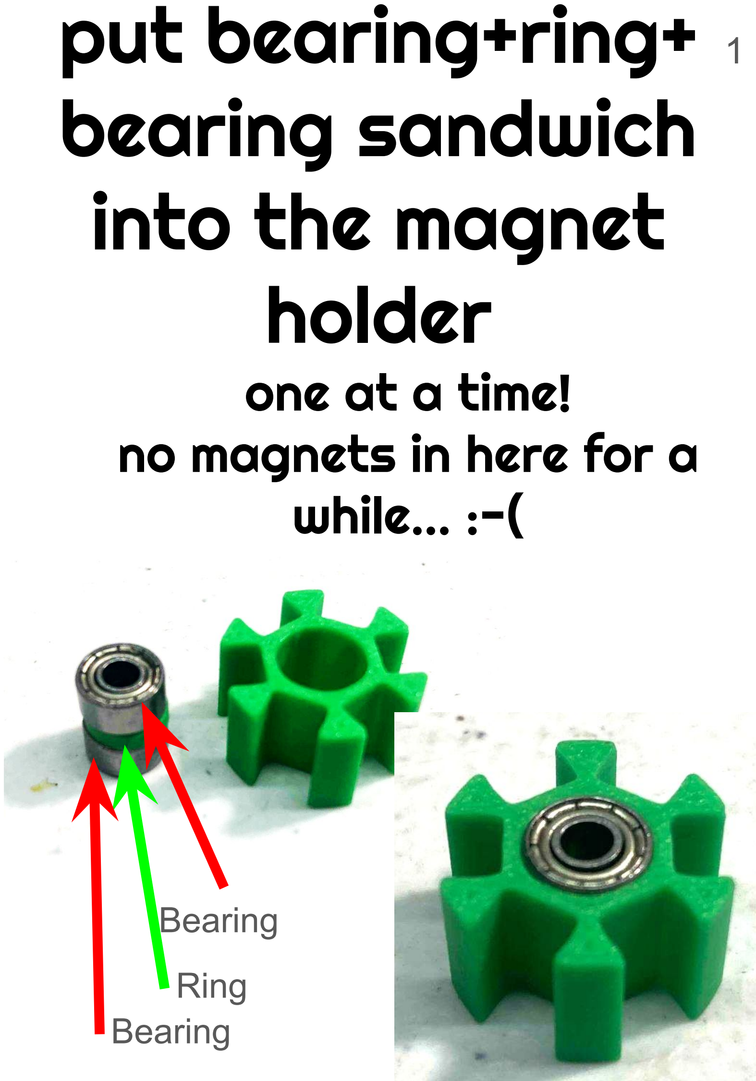
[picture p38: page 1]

# into the magnet holder

# one at a time! no magnets in here for a while… :-(

Ring

Bearing

Bearing

# magnet ring assembly

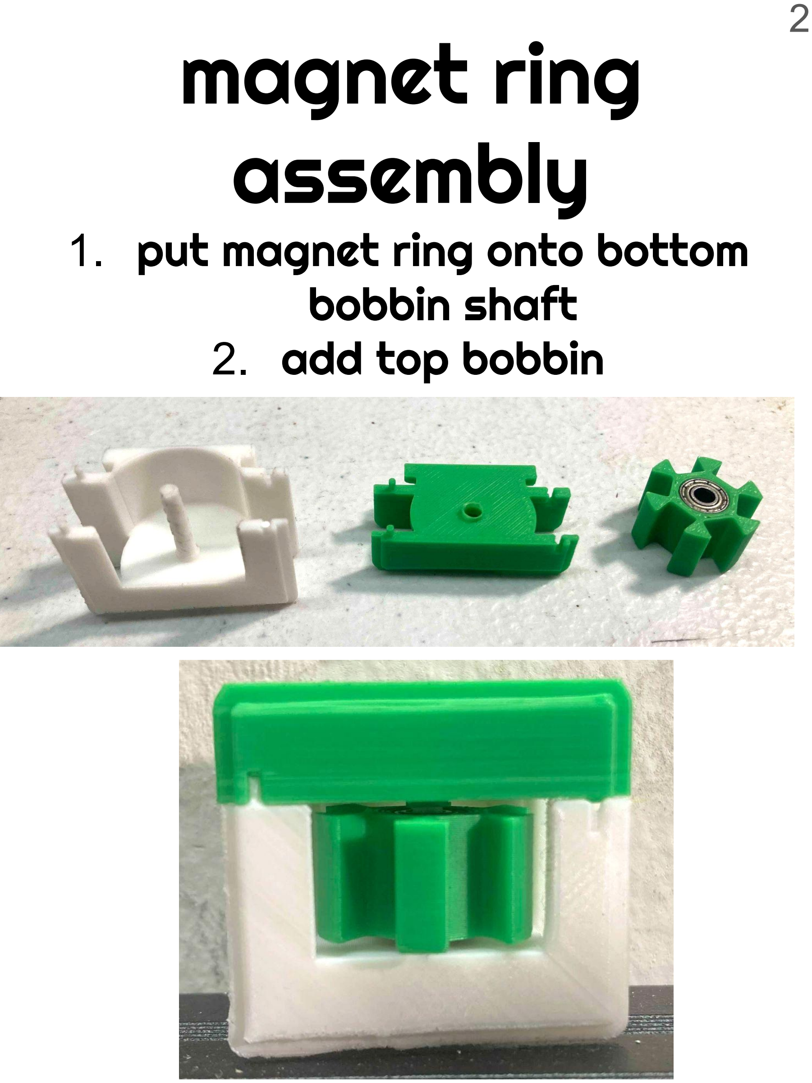
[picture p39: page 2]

## 1. put magnet ring onto bottom bobbin shaft 2. add top bobbin

# Wire Prep

## 1. feed magnet wire through

inside | hole | in bobbin (notice

## the hole above it too!) 2. pull ~5-6” (15cm) through

3. do about 20 turns by hand.
a. make the loops tight, not loose!

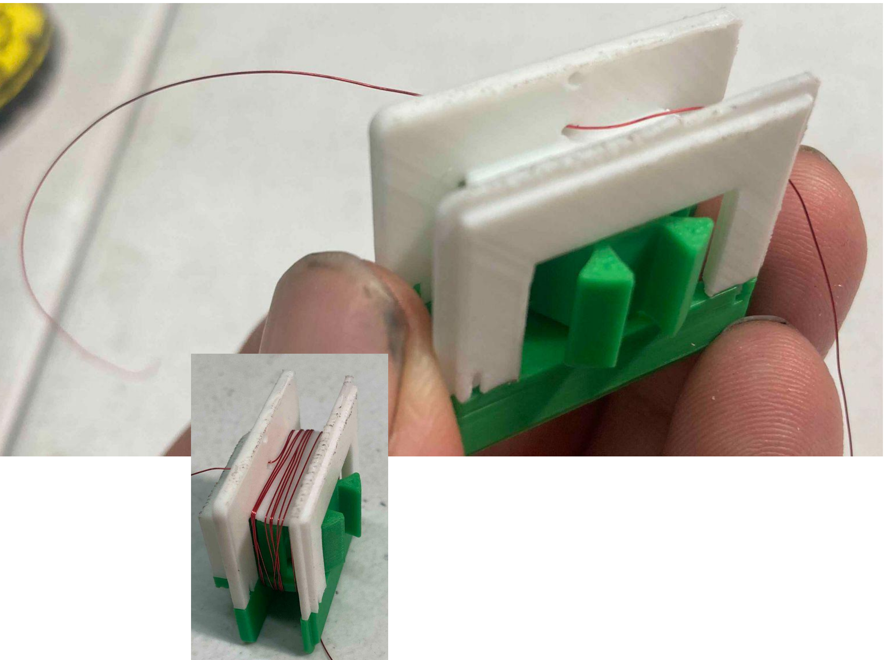
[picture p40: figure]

# 1. slide this assembly into

the winding attachment.

# 2. put in the M4 screw and

nut (hand tight) to lock.

# 3. wrap the excess 6” of wire around the end of the screw (so it is not in the way)

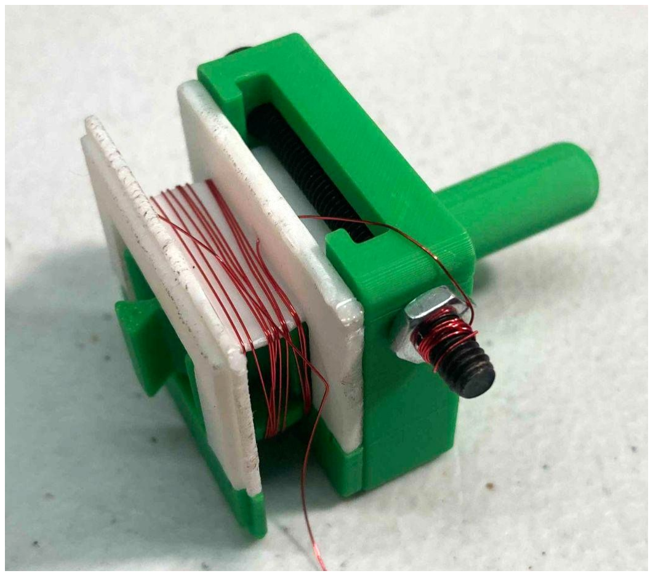
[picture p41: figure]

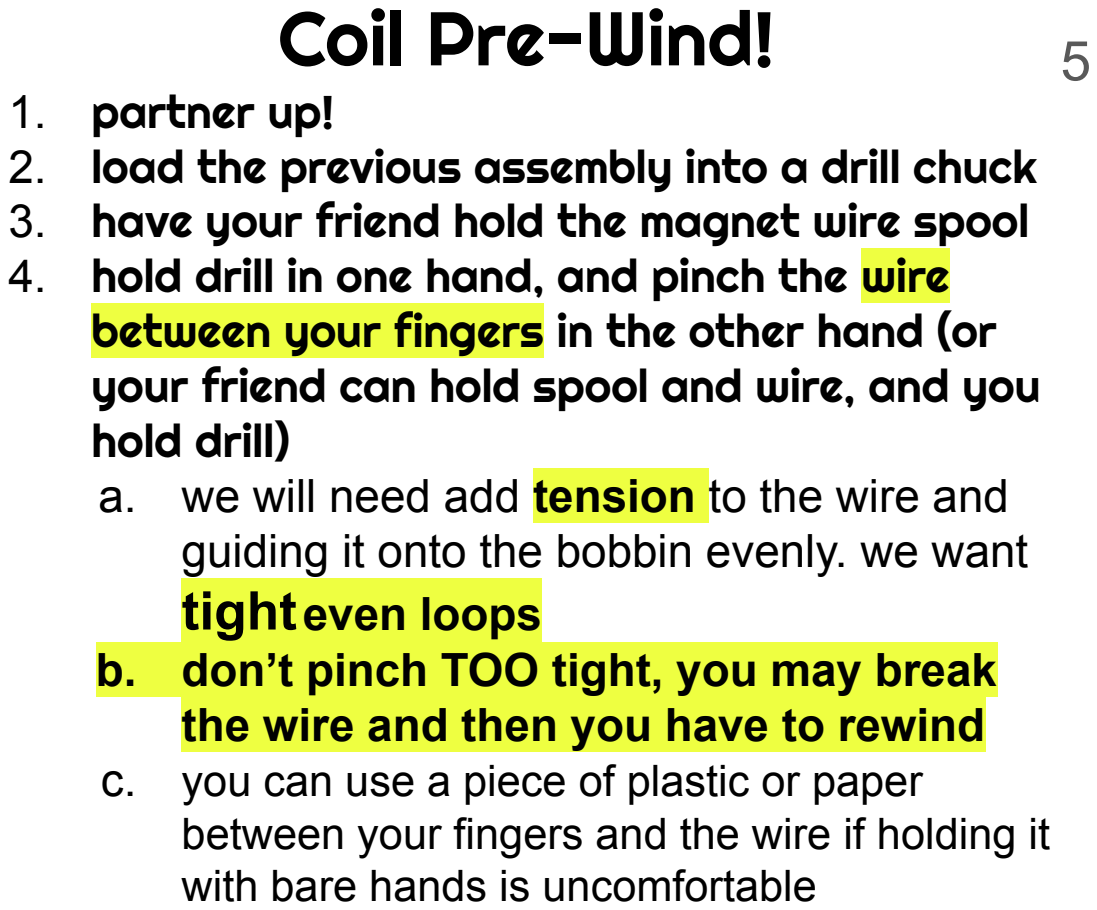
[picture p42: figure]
Coil Pre-Wind!; 1. partner up!; hold drill); tighteven loops b. don’t pinch TOO tight, you may break the wire and then you have to rewind; with bare hands is uncomfortable

2. load the previous assembly into a drill chuck
3. have your friend hold the magnet wire spool
4. hold drill in one hand, and pinch the wire between your fingers in the other hand (or your friend can hold spool and wire, and you
a. we will need add tension to the wire and guiding it onto the bobbin evenly. we want
c. you can use a piece of plastic or paper between your fingers and the wire if holding it

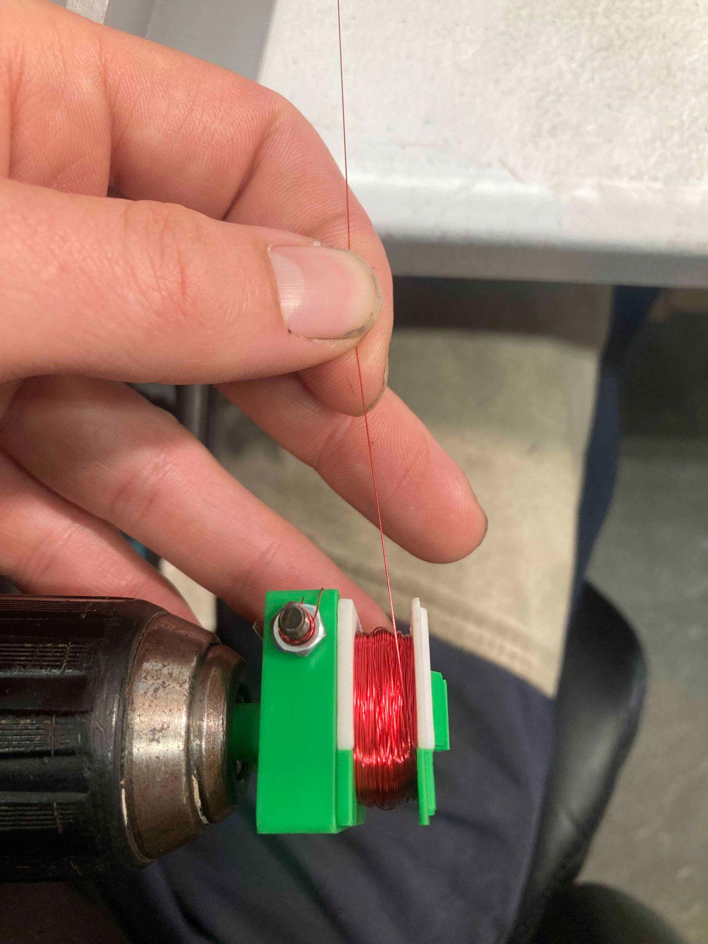
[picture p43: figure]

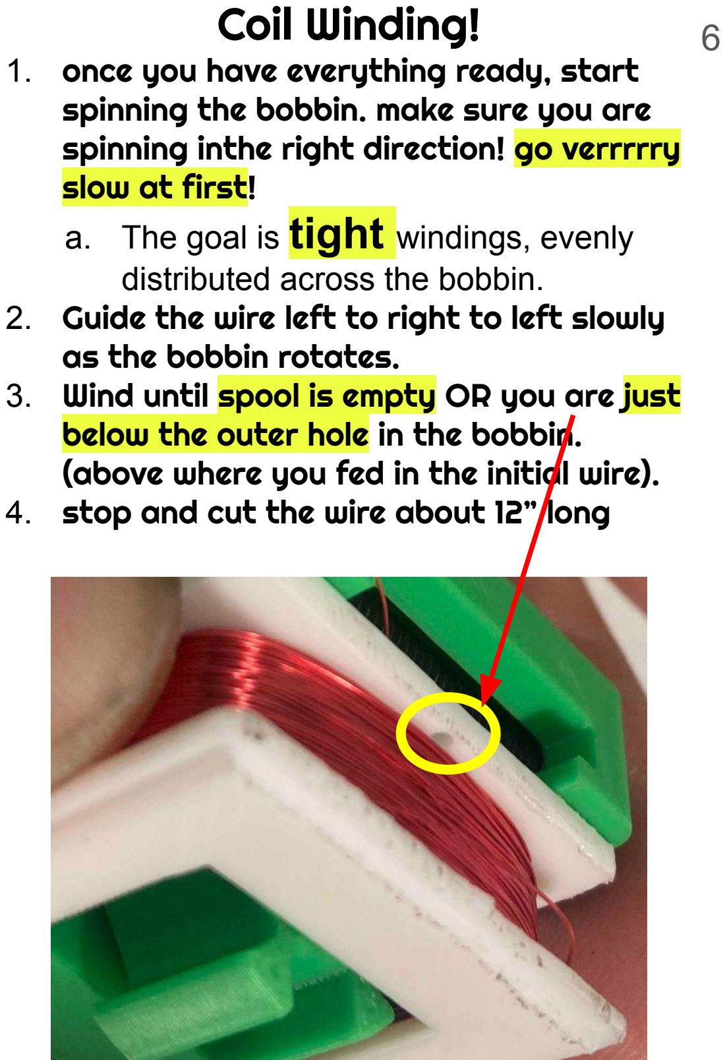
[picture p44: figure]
Coil Winding!; spinning the bobbin. make sure you are; slow at first!; a. The goal is tight windings, evenly; distributed across the bobbin.; as the bobbin rotates.; below the outer hole in the bobbin.; 4. stop and cut the wire about 12” long

1. once you have everything ready, start

spinning inthe right direction! go verrrrry

2. Guide the wire left to right to left slowly
3. Wind until spool is empty OR you are just

(above where you fed in the initial wire).

# remove bobbin from attachment

## 1. unwind excess wire from screw 2. take out nut and screw 3. remove bobbin 4. wind the wire around the

bobbin 6 or so times tightly.

## 5. feed the wire through the upper hole

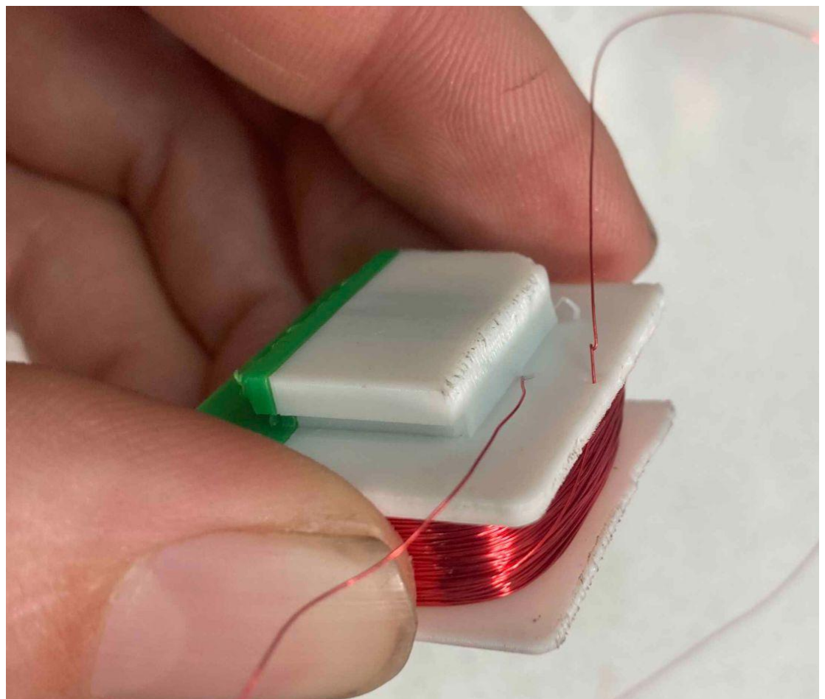
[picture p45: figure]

# Coil Installation

1. cut both wires down to ~ 3” (7 cm).

## 2. feed wire through the slot in bottom of the main enclosure 3. slide bobbin onto enclosure with wires coming out bottom

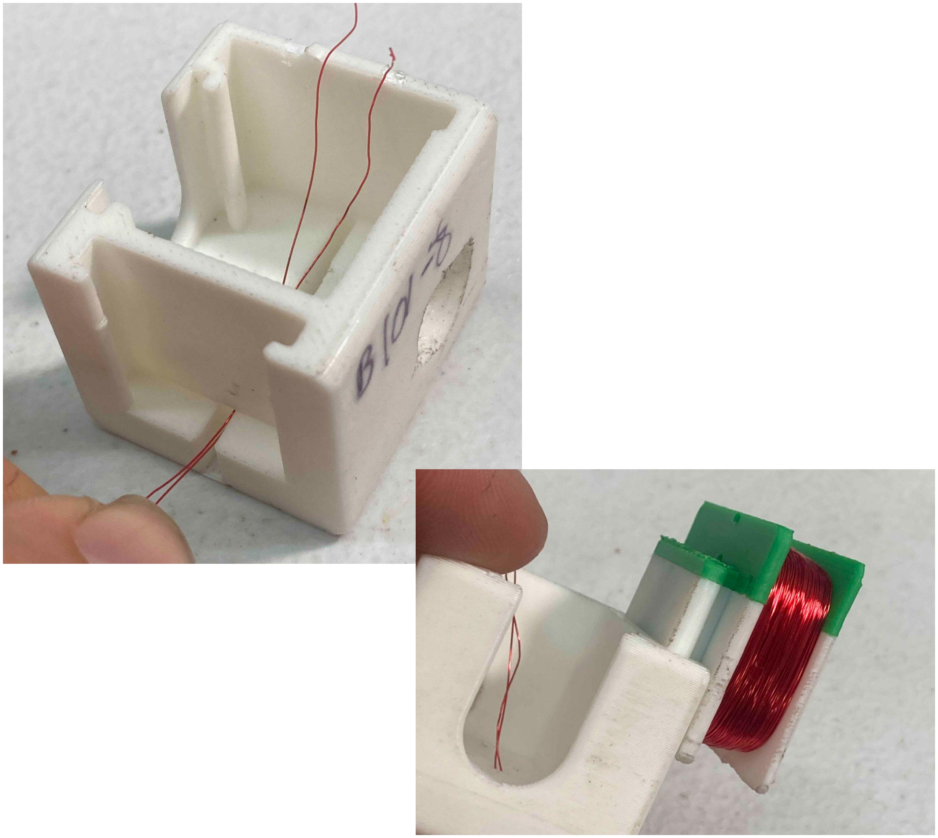
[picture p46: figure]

# COIL PCB wiring

1. use sandpaper to sand off about ¼” off the ends of the wires.
2. the color should wipe off and you see bare copper.
3. Loosen the small screw (using the small flathead screwdriver) on the green connector on the rectifier PCB.
4. We will be putting the wires into this connector.
5. fold about ⅛” back of each wire. (making a shepherds hook-type situation)
6. put the wire into one of the small holes on the side of the green connector. tighten with screwdriver.
7. Add the other wire to the remaining hole on the connector. Tighten with screwdriver.

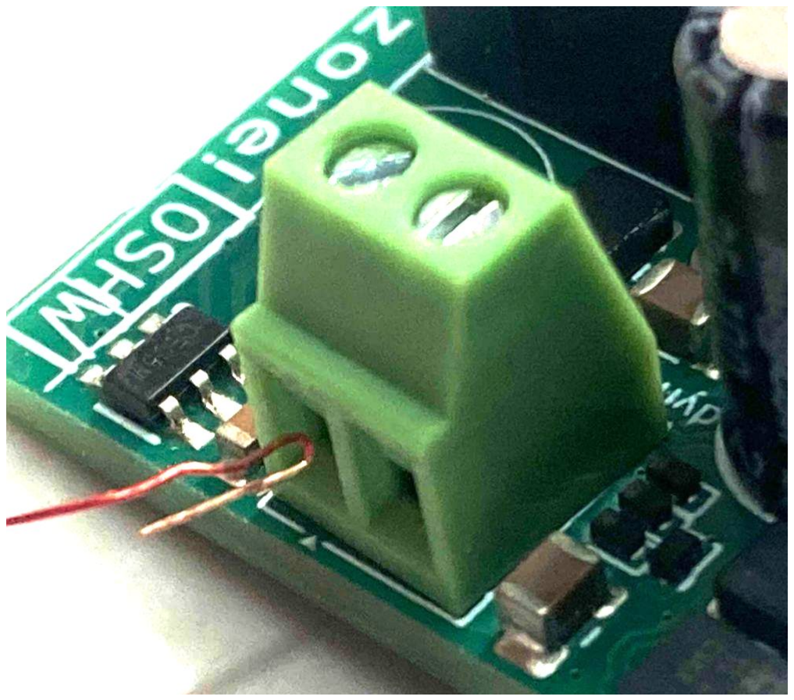
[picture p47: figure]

# PCB Installation

# 1. Side PCB into the rear

of the enclosure,

# making sure the green connector is facing up!

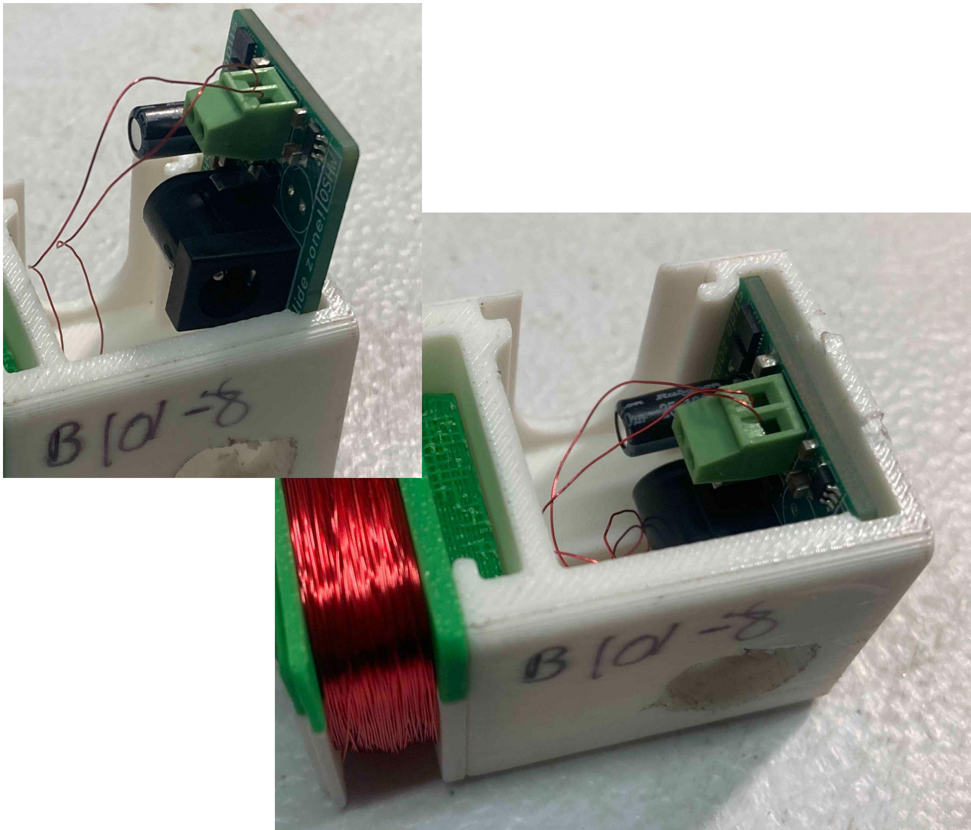
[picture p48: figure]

## Assemble bike mount! Pt. 1

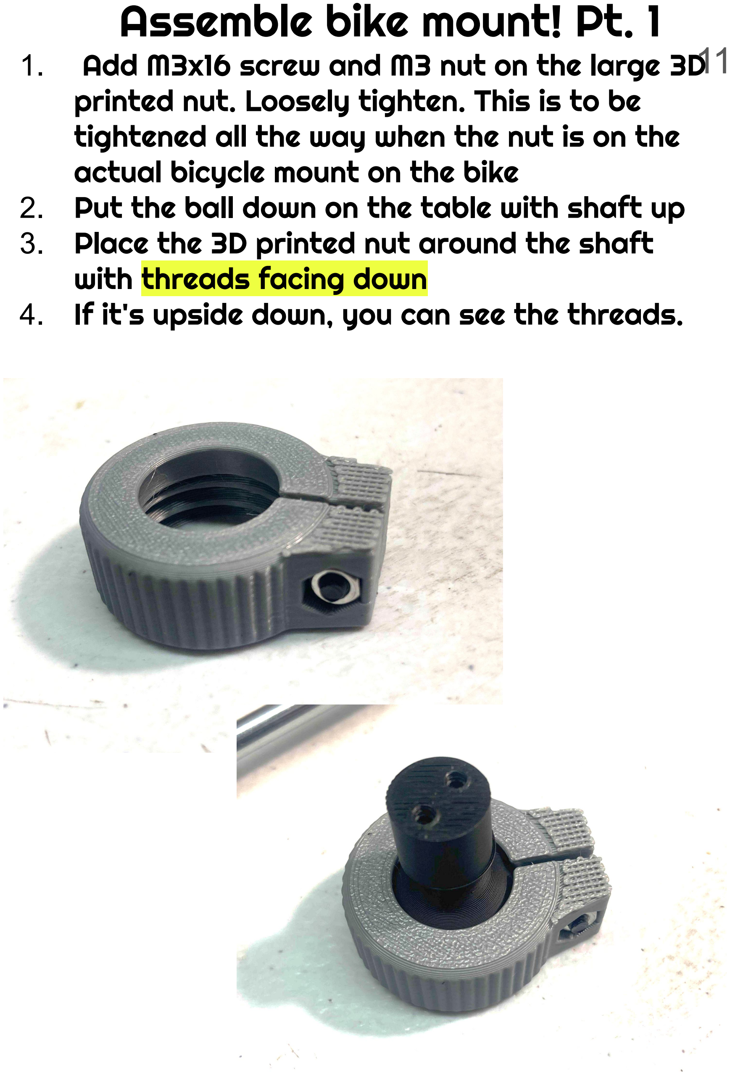
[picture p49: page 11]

1. Add M3x16 screw and M3 nut on the large 3D printed nut. Loosely tighten. This is to be tightened all the way when the nut is on the actual bicycle mount on the bike
2. Put the ball down on the table with shaft up
3. Place the 3D printed nut around the shaft with threads facing down
4. If it's upside down, you can see the threads.

## Assemble bike mount! Pt 2

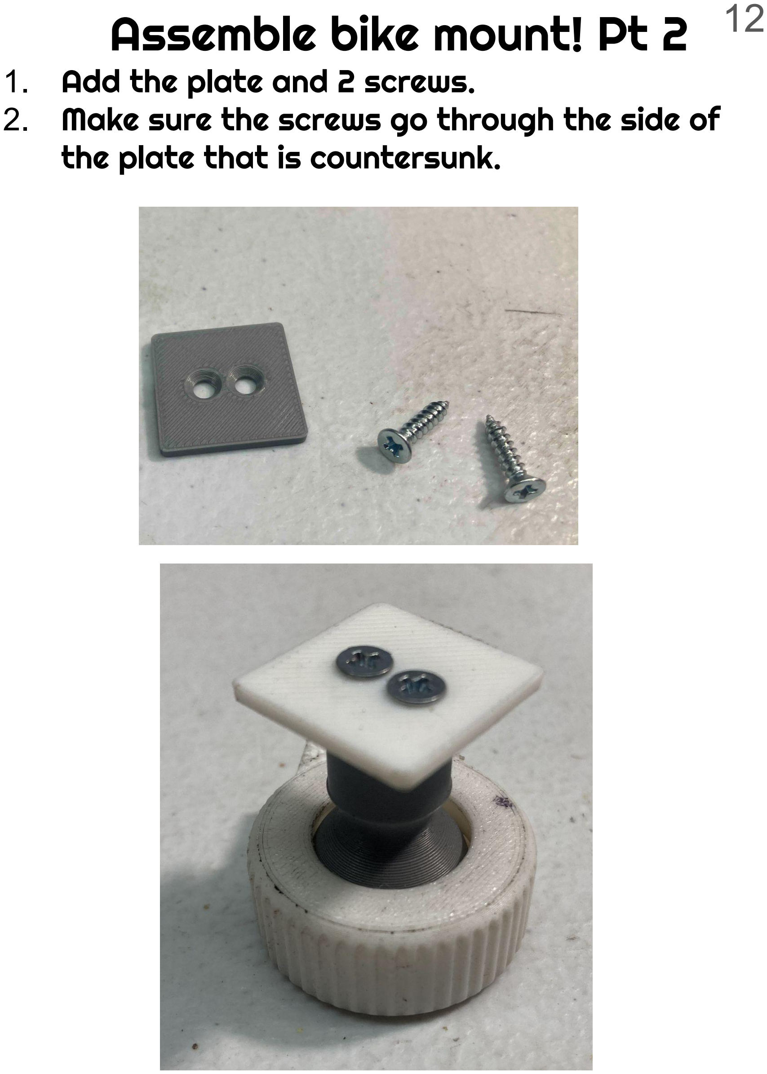
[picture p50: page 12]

1. Add the plate and 2 screws.
2. Make sure the screws go through the side of the plate that is countersunk.

## Assemble bike mount! Pt 3

## 1. Screw in the ball nut into the

bike mount.

## 2. slide this assembly onto the enclosure 3. Add Cover

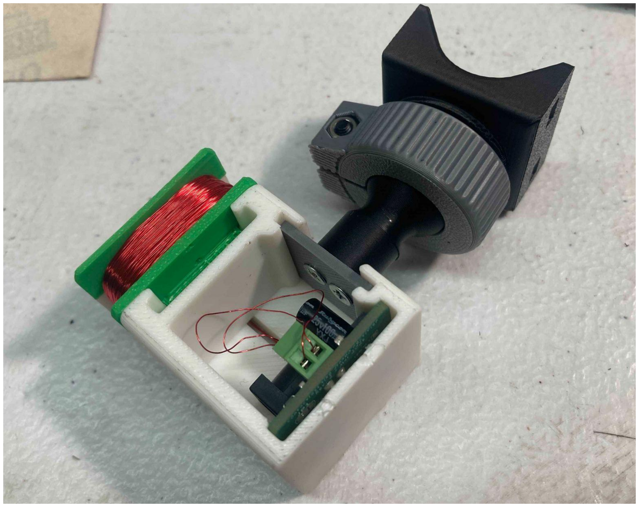
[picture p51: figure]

# Add Magnets to Magnet Ring!

caution! These are very strong!
1. Pull off 2 magnets from the magnet stack
2. Put these two into a slot on the magnet ring
3. Pull off 2 more magnets
4. Flip these and put in the slot next to the first two.
a. test by holding the pair close to the previous one and seeing if they attract or repel.
b. if they repel that is good, put them into the next slot that way. if not, flip them
5. do this for the remaining slots

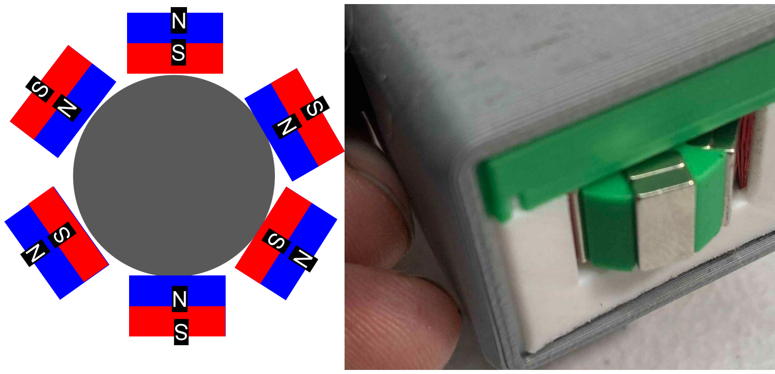
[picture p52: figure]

# Assemble Light!

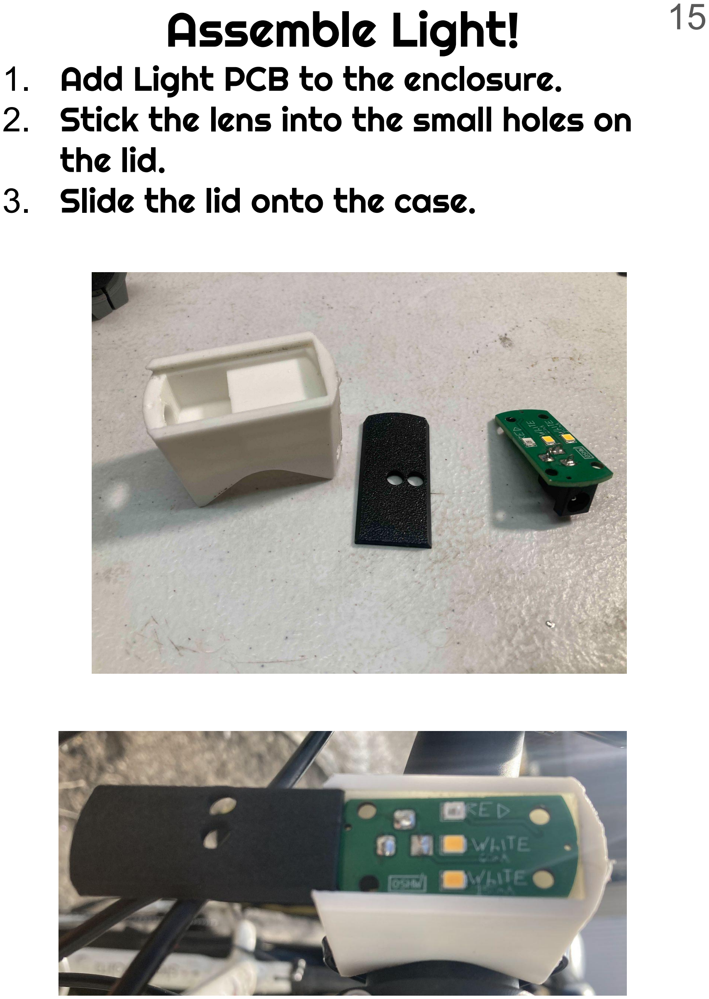
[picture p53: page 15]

1. Add Light PCB to the enclosure.

### 2. Stick the lens into the small holes on

the lid.
3. Slide the lid onto the case.

## Mounting!

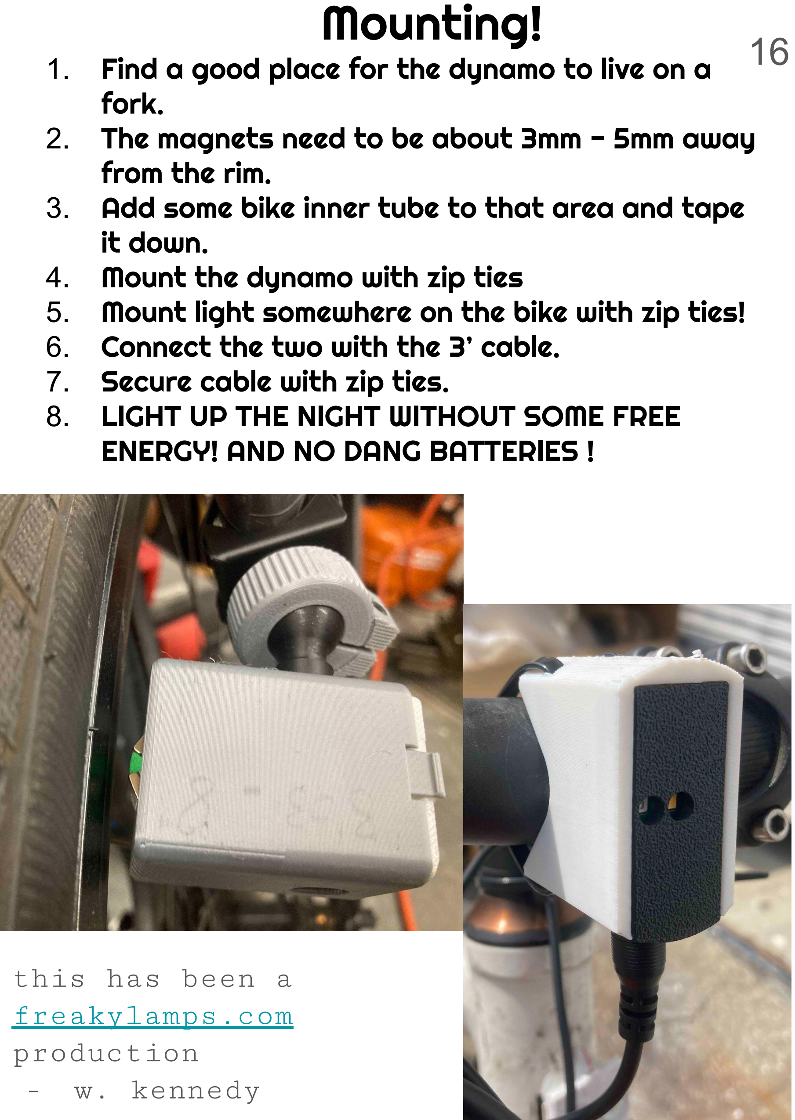
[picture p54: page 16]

1. Find a good place for the dynamo to live on a fork.
2. The magnets need to be about 3mm - 5mm away from the rim.
3. Add some bike inner tube to that area and tape it down.
4. Mount the dynamo with zip ties
5. Mount light somewhere on the bike with zip ties!
6. Connect the two with the 3’ cable.
7. Secure cable with zip ties.
8. LIGHT UP THE NIGHT WITHOUT SOME FREE ENERGY! AND NO DANG BATTERIES !

this has been a
freakylamps.com
production
- w. kennedy

# contactless bicycle dynamo workshop!

# Make a bicycle light without a battery!

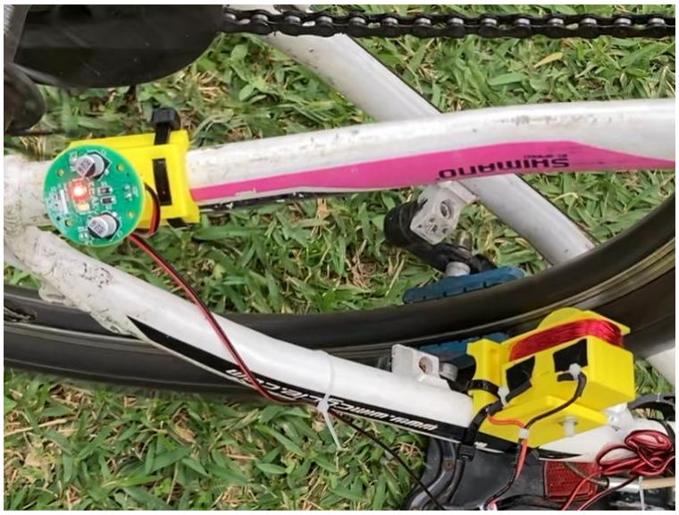
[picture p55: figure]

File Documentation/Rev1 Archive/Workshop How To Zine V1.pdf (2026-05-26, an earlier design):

# add M5 screw in the back of dynamo housing

## - Use flathead screwdriver to get the screw through the hole

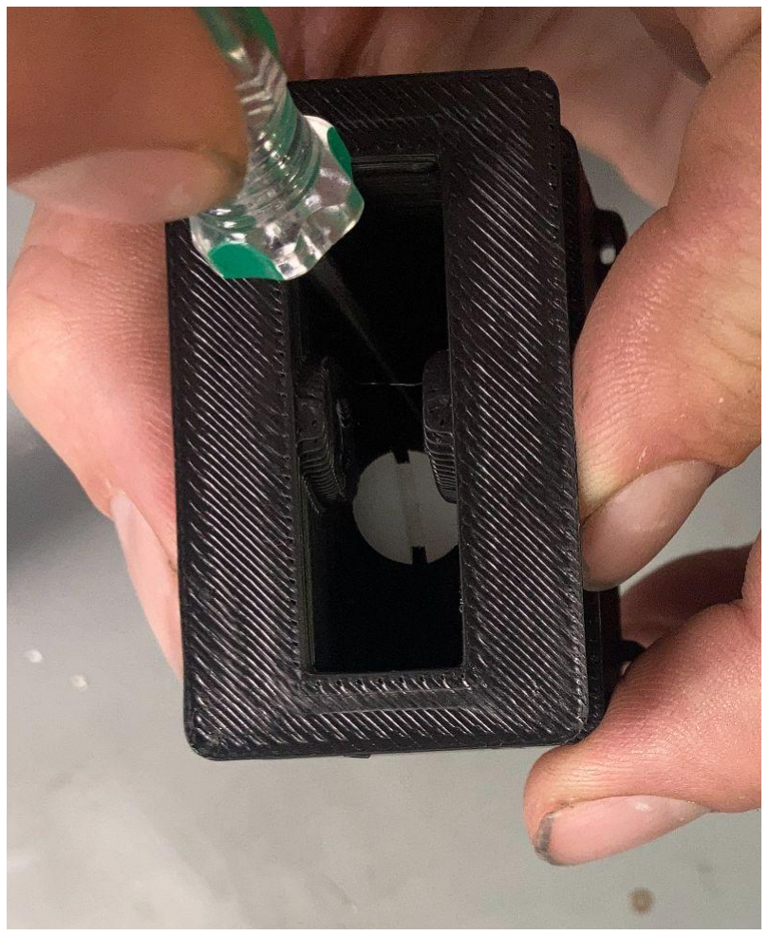
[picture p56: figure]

# Add M5 nut to back and screw in

### - when done screwing in, use wire stripper / pliers to really tighten the screw down on the nut

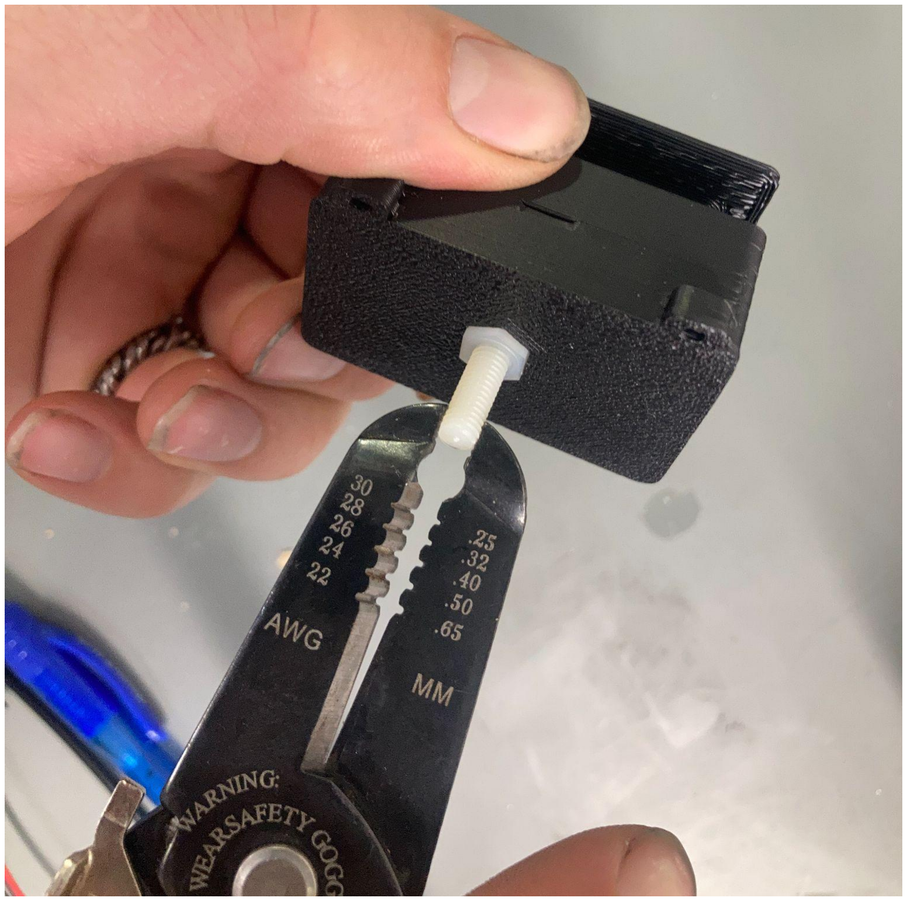
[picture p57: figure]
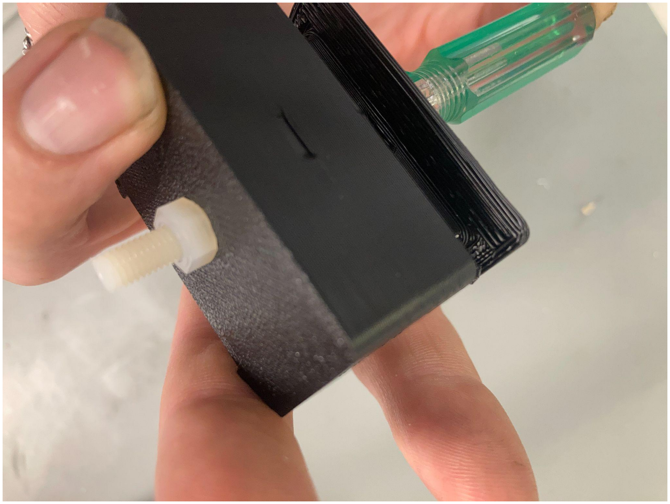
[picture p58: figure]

## - add M5 adaptor to the bearing (sometimes you need to hit it with a hammer to get it in) - add magnet ring around bearing

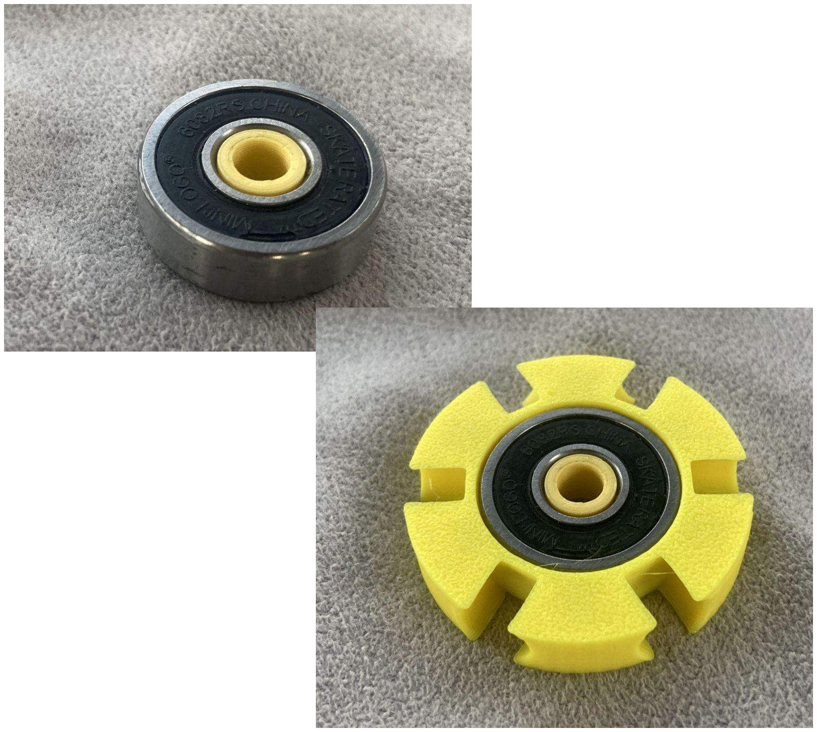
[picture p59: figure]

# add magnets!

## - two stacked magnets per slot - make sure adjacent ones are opposite polarity!

(they need to push away from each other.
test magnets you are about to place by trying to stick them to the magnets next to them. if they stick, flip them!)

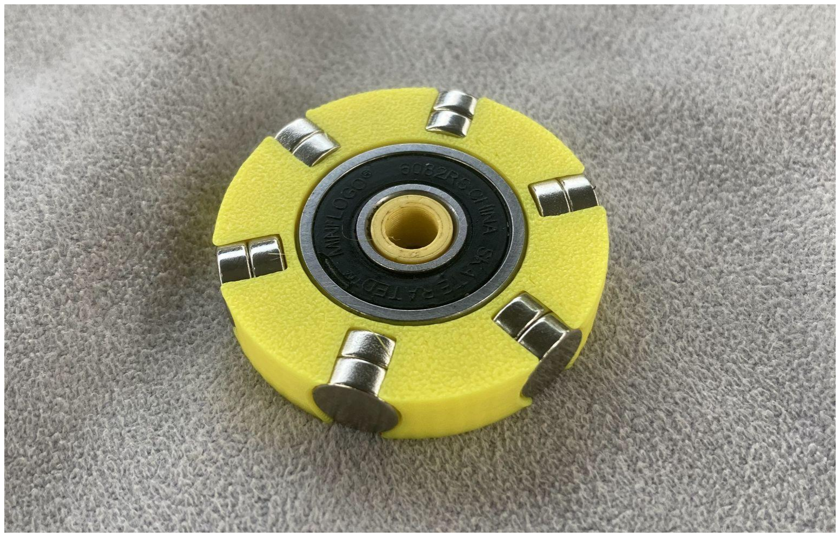
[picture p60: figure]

## - stick bearing assembly into Dynamo Housing - add screw through assembly - add nut on back side (nut should fit in hexagonal hole) - Tighten!

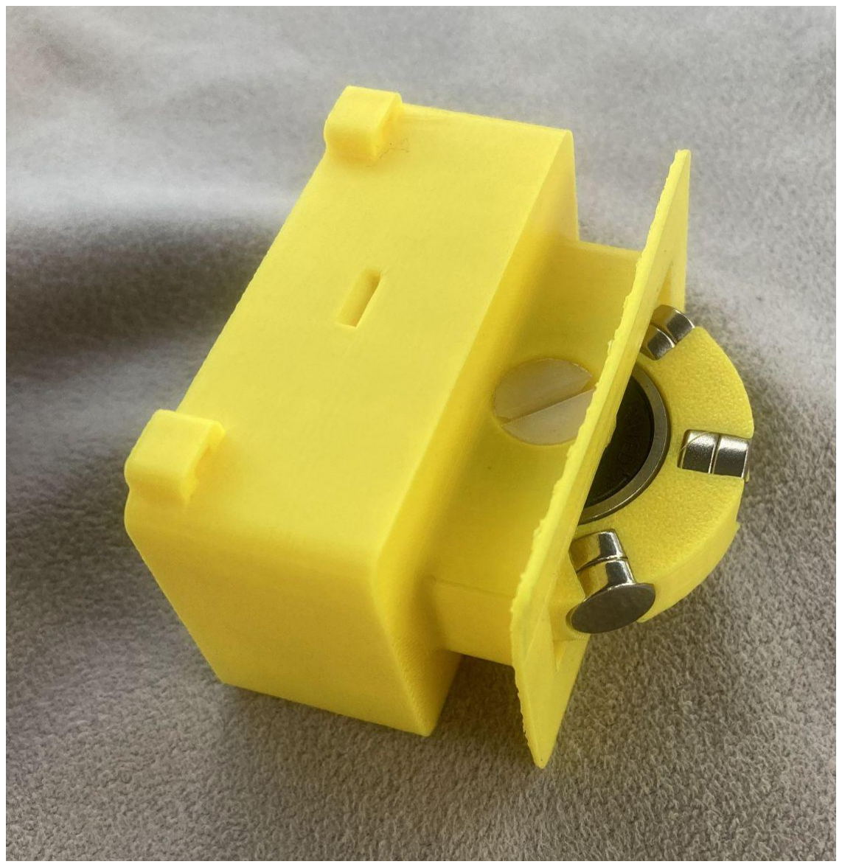
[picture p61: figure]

# prepare winding

### - cut small piece of electrical tape - tape one side of enameled wire to dynamo housing

- do a couple windings by hand,

### keep them tight!

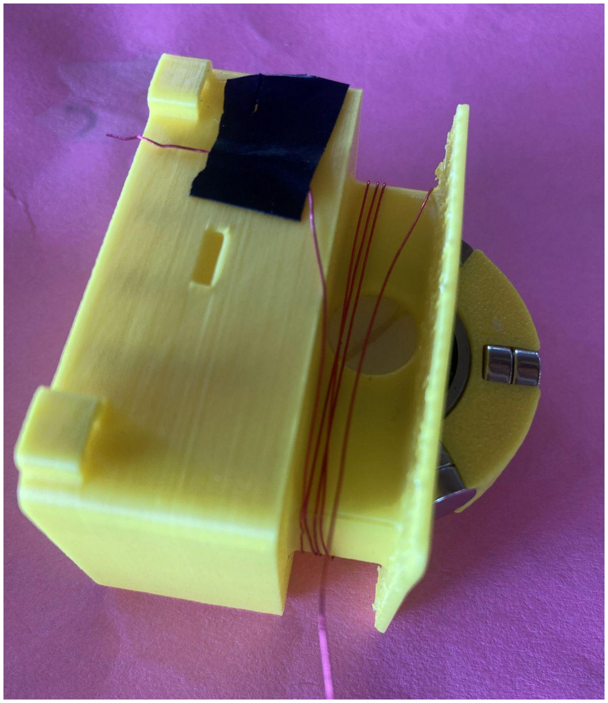
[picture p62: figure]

# winding!

- put that screw poking out of the back of the dynamo into the drill chuck
- someone holds drill
- other person holds spool and helps guide it in
- start slow!
- having the spool be far away from the drill can help

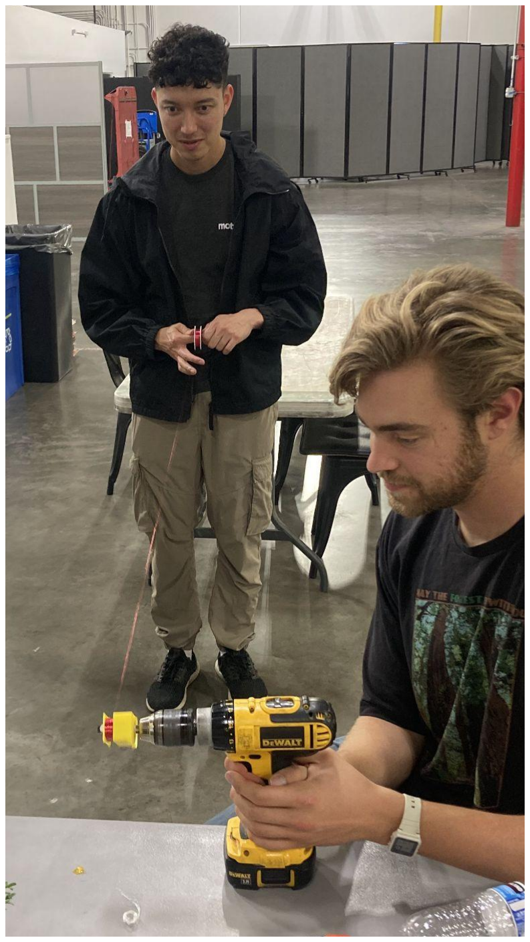
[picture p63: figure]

## - when done unwinding the entire spool, tape the other wire to dynamo to temporarily secure - scrape enamel off with knife or sandpaper

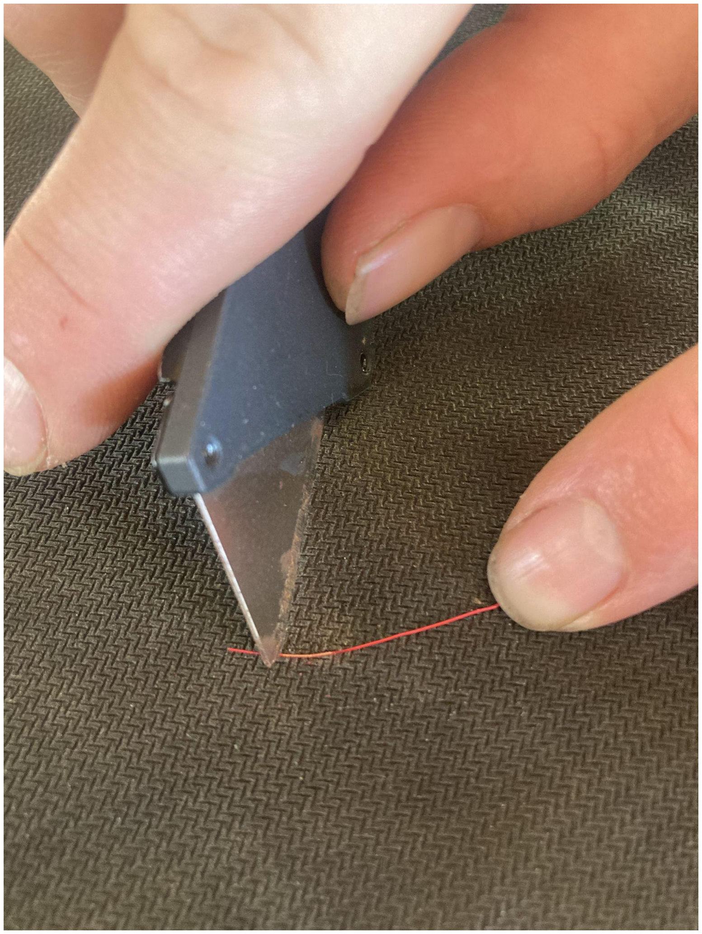
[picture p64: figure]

## solder JST connector to the enamel wire - make sure to use shrink wrap! - secure with zip ties

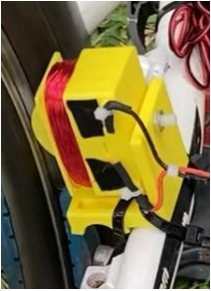
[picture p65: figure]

## do you want the bike light to be red or white? - solder blob the corresponding jumper

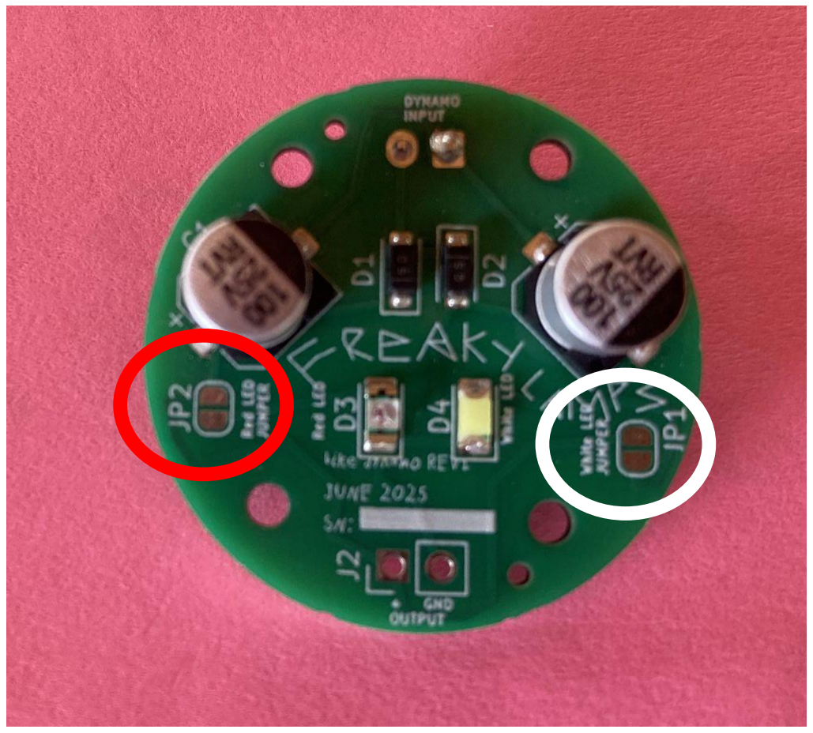
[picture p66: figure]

# LIGHT TIME! put lens on the PCB cover with a lil super glue

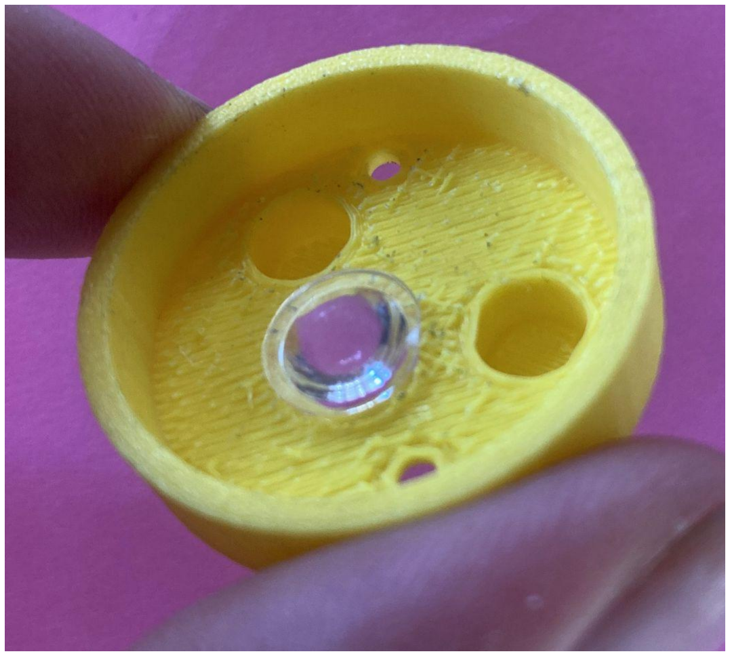
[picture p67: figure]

# put PCB on the bike mount

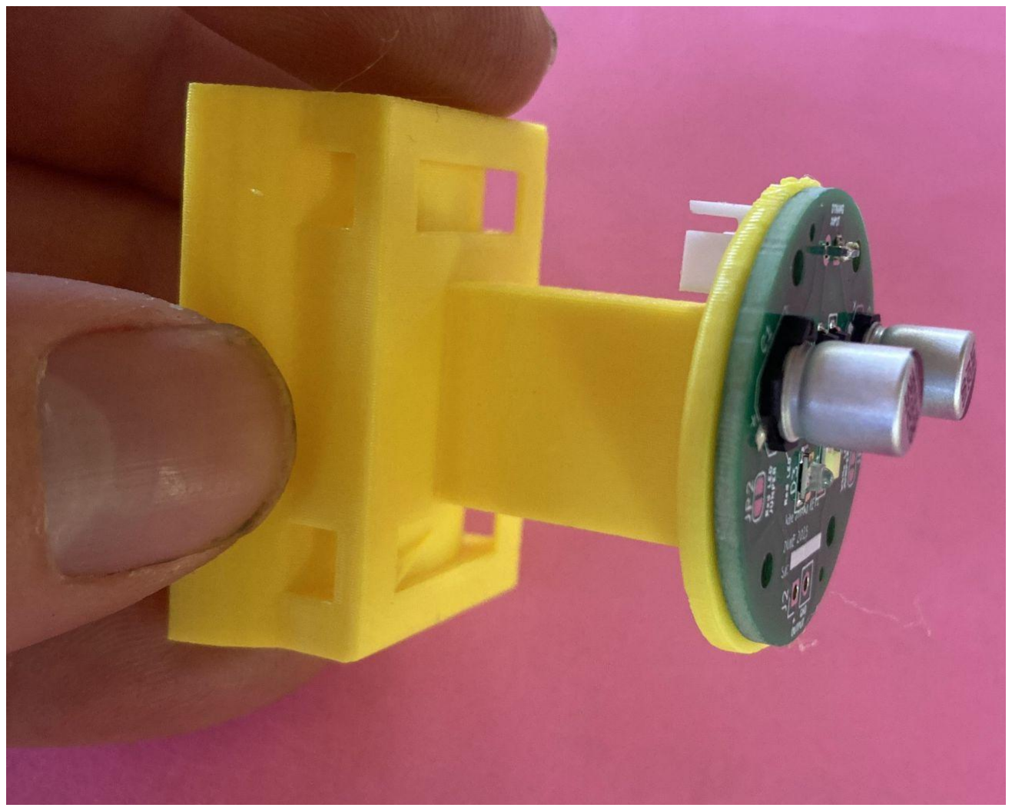
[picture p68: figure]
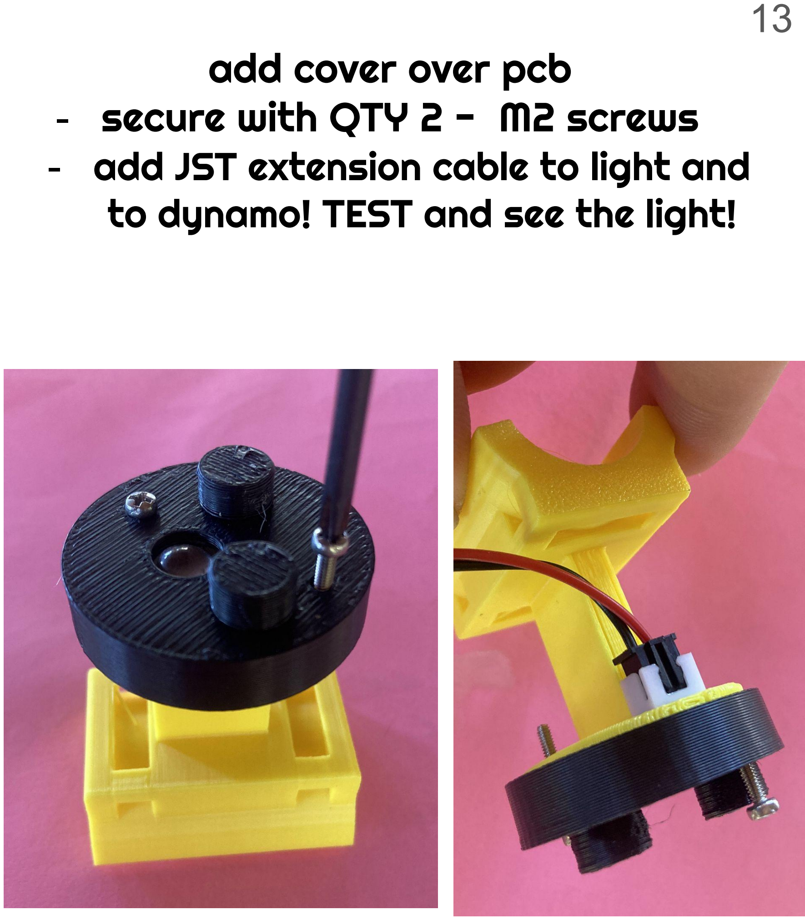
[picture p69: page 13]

add cover over pcb
- secure with QTY 2 - M2 screws
- add JST extension cable to light and to dynamo! TEST and see the light!

# attach Dynamo to bike mount with M5 nut

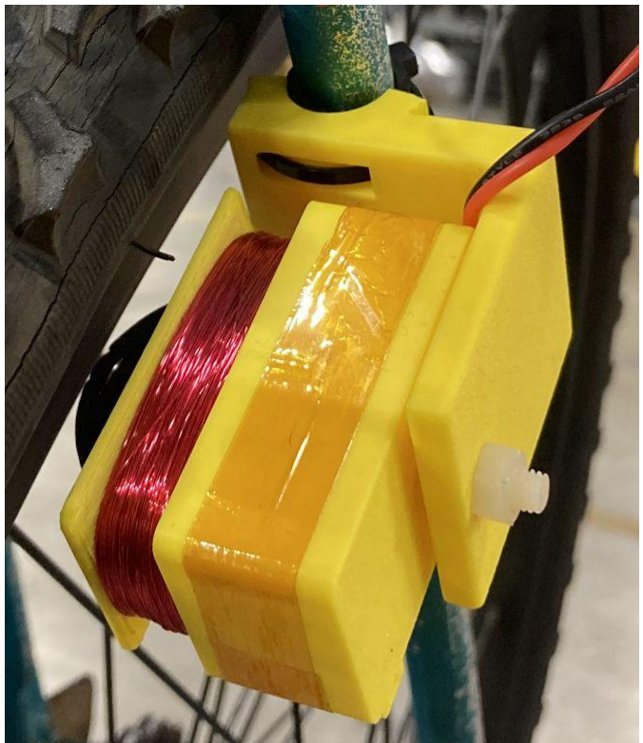
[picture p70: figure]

- mount dynamo to bike with zipties! (add an old inner tube or piece of rubber down on the rod first so it doesn't slide around)
- get it as close to the aluminum rim as you can, but dont touch it!
- Mount bike light to bike! (also add inner tube/rubber on rod)

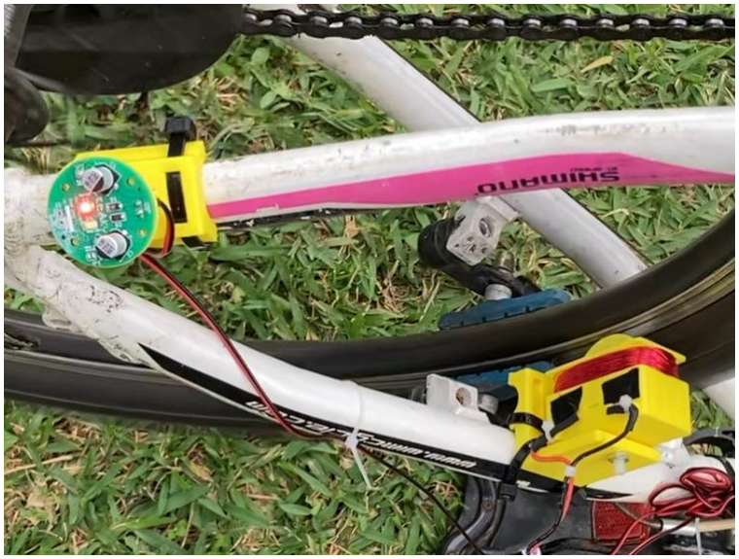
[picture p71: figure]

# once you know its working, add the protective cover over the dynamo

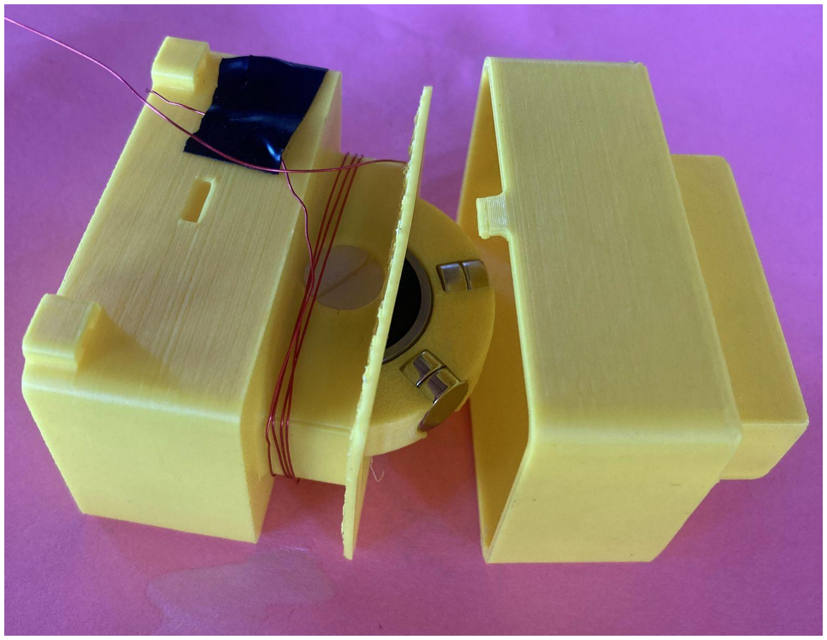
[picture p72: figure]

# contactless bicycle dynamo workshop!

# Make a bicycle light without a battery!


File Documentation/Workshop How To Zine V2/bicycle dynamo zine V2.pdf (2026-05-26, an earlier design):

# put bearing+ring+ bearing sandwich into the magnet holder

# one at a time! no magnets in here for a while… :-(

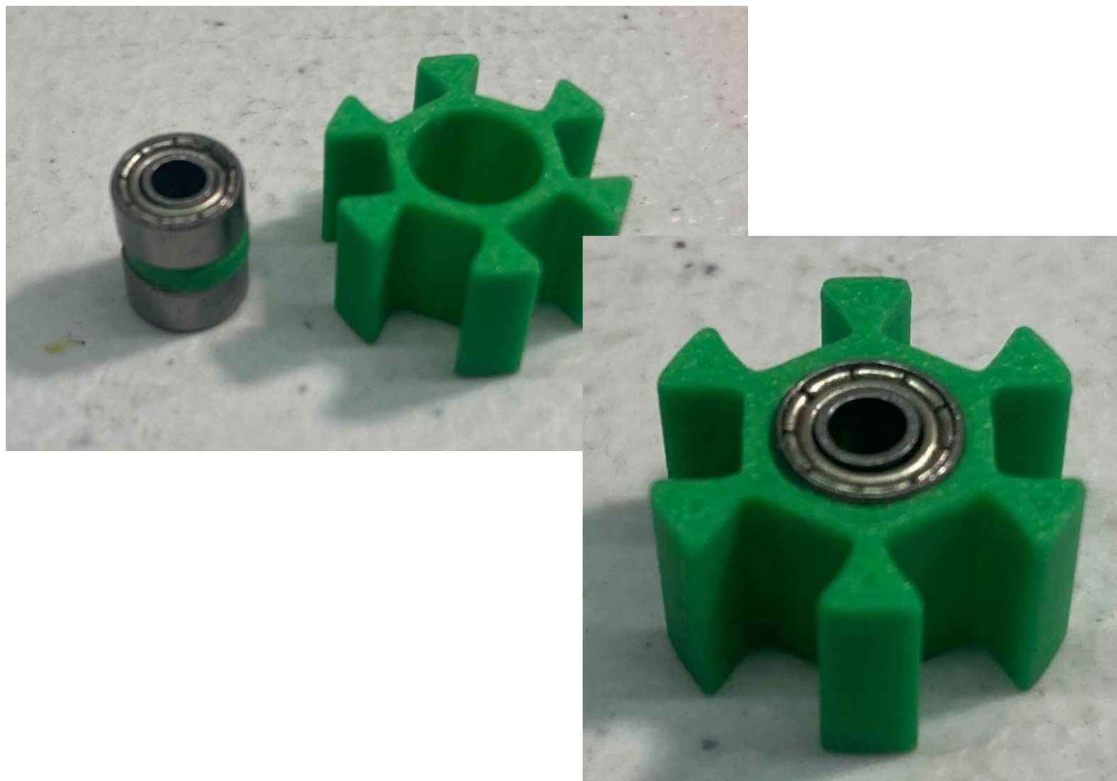
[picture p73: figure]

# magnet ring assembly

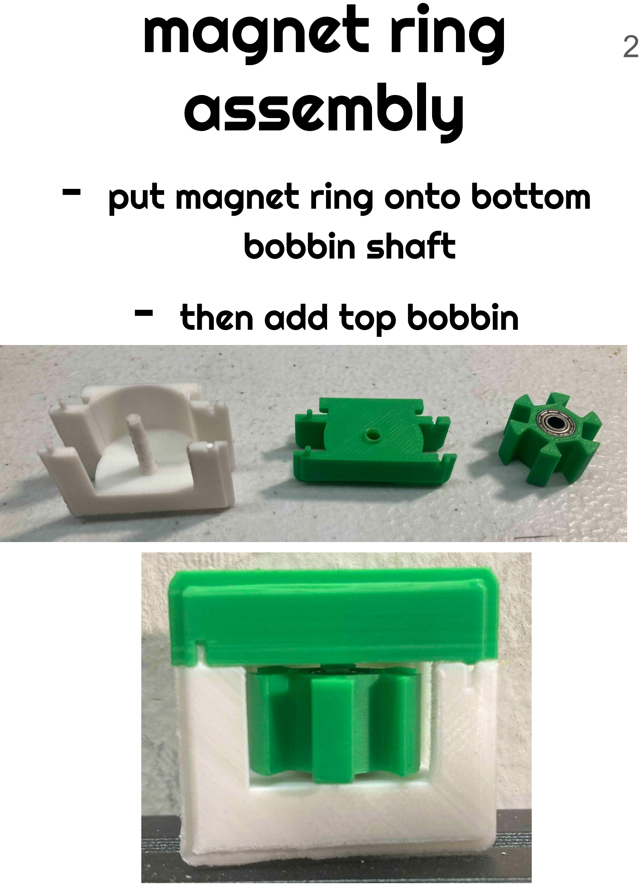
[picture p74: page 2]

## - put magnet ring onto bottom bobbin shaft - then add top bobbin

# Wire Prep

## - feed magnet wire through

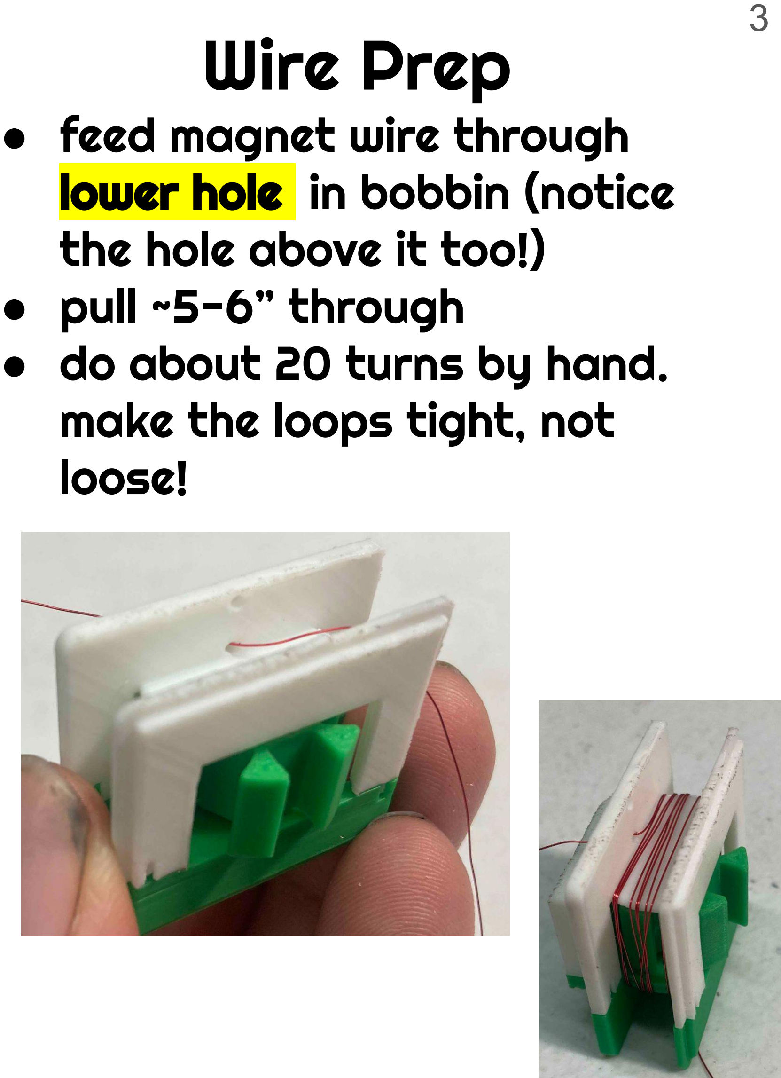
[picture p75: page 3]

## lower hole in bobbin (notice the hole above it too!) - pull ~5-6” through

- do about 20 turns by hand.

## make the loops tight, not loose!

# - slide this assembly into

the winding attachment.

# - put in the M4 screw and

nut (hand tight) to lock.

# - wrap the excess 6” of wire around the end of the screw so it is not in the way


# Coil Pre-Wind!

- load the previous assembly into a drill chuck
- have a friend hold magnet wire spool, or put on the spool holder
- we need to add tension to the wire and guide it onto the bobbin evenly,
- I typically use my hand for this, so you usually need to hold the wire between your fingers and add tension and guide it left to right. (you can also use a piece of plastic or paper btw your fingers and the wire)

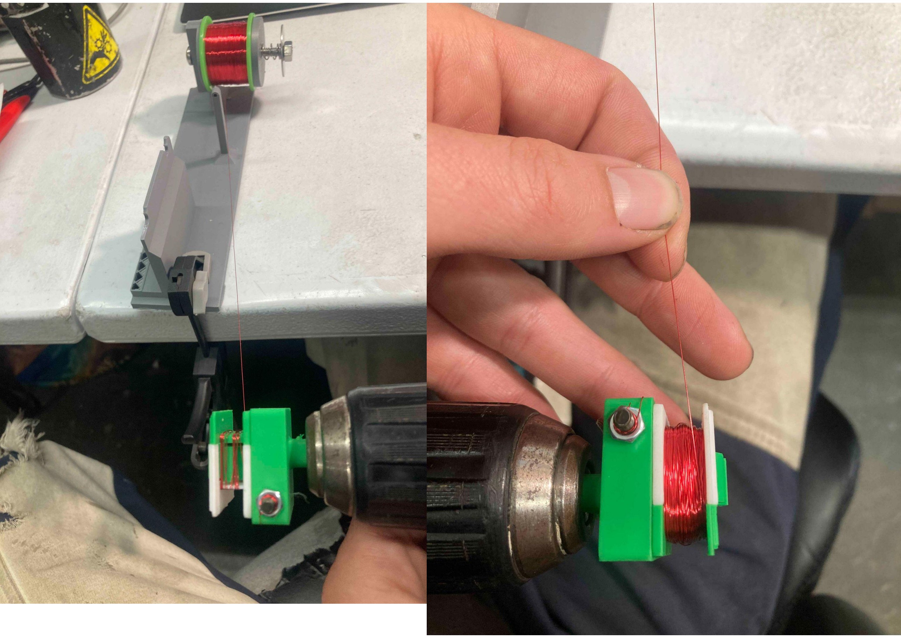
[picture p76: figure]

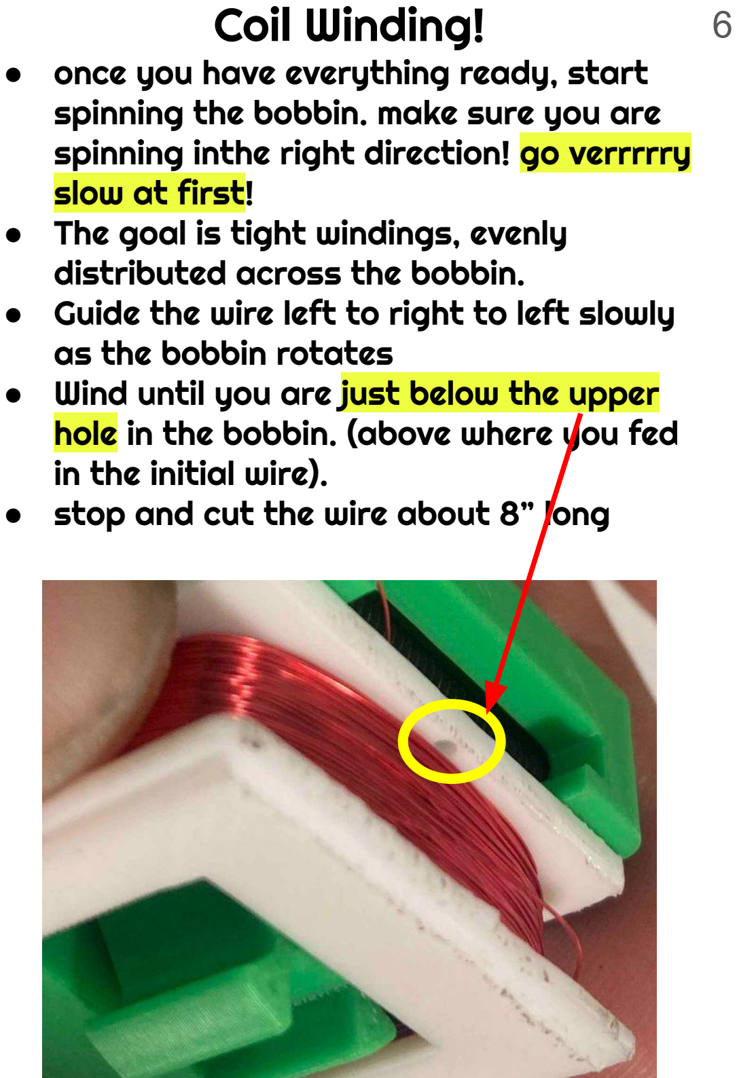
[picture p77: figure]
Coil Winding! ● once you have everything ready, start spinning the bobbin. make sure you are; slow at first! ● The goal is tight windings, evenly distributed across the bobbin.; as the bobbin rotates; in the initial wire). ● stop and cut the wire about 8” long

spinning inthe right direction! go verrrrry

- Guide the wire left to right to left slowly
- Wind until you are just below the upper hole in the bobbin. (above where you fed

# remove bobbin from attachment

## - unwind excess wire from screw - take out nut, screw

- remove bobbin.

## - wind the wire around a

couple times tightly.

## - feed it through the upper hole


# Coil Installation

- cut wire down to ~ 3”.

## - feed wire through the slot in bottom of the main enclosure - slide bobbin onto enclosure with wires coming out bottom


# COIL PCB wiring

- use sandpaper to sand off about ¼” off the ends of the wires.
- the color should wipe off and you see bare copper.
- Loosen the small screw (using the small flathead screwdriver) on the green connector on the rectifier PCB.
- We will be putting the wires into this connector.
- fold about ⅛” back of each wire. put the wire into one of the small holes on the side of the green connector. tighten.
- Add the other wire to the remaining hole on the connector.


# PCB Installation

# - Side PCB into the rear

of the enclosure,

# making sure the green connector is facing up!


Assemble dynamo mount! ● Add M3x16 screw and M3 nut on the large 3D printed nut. ● Put the 3D printed nut around the shaft


- Make sure it it in can go around the ball nicely.
- If it's upside down, you can see the threads.

## Assemble dynamo mount!


- Add the plate and 2 screws.
- Make sure the screws go through the side of the plate that is countersunk.

## - Screw in the ball nut into the

bike mount.

## - slide this assembly onto the enclosure


# Add Magnets to Magnet Ring!

## - caution! These are very strong!

- 2 magnets per slot.

## - make sure each pair of magnets is opposite polarity from the one

before.

## - test by holding the pair close to the previous one and seeing if

they attract or repel.

## - if they repel that is good, put

them into the next slot that way. if not, flip them.


# Assemble Light!

- Add Light PCB to the enclosure.

### - Stick the lens into the small holes on

the lid.
- Slide the lid onto the case.
- There is a way to get red light out of this PCB, but it is annoying, so we will just be using white light. If you really want red, it requires some delicate knife work and a few wires to solder. maybe wait for V2….


## Mounting!

- Find a good place for the dynamo to live on a fork.
- The magnets need to be about 3mm - 5mm away from the rim.
- Add some bike inner tube to that area and tape it down.
- Then mount the dynamo with zip ties
- Mount light somewhere on the bike with zip ties!
- Connect the two with the 3’ cable.
- Secure cable with zip ties.
- LIGHT UP THE NIGHT WITHOUT SOME FREE ENERGY! AND NO DANG BATTERIES !


# contactless bicycle dynamo workshop!

# Make a bicycle light without a battery!


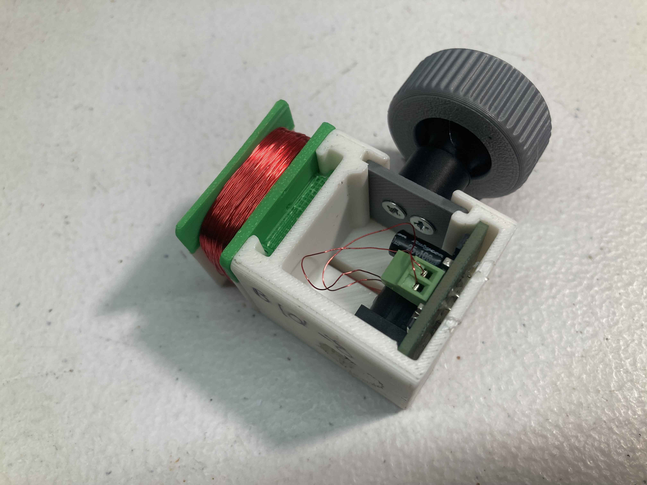
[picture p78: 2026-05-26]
Documentation/Workshop How To Zine V2/photos/Photos-3-001/IMG_7963.jpg

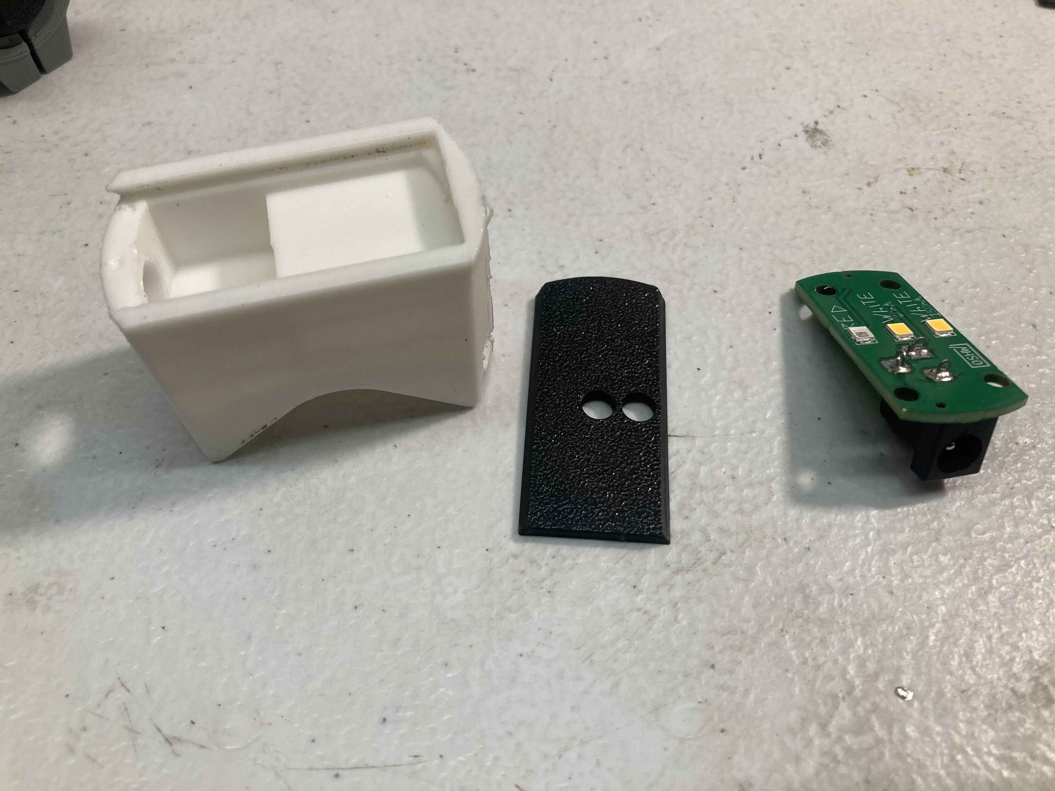
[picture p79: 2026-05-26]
Documentation/Workshop How To Zine V2/photos/Photos-3-001/IMG_7971.jpg

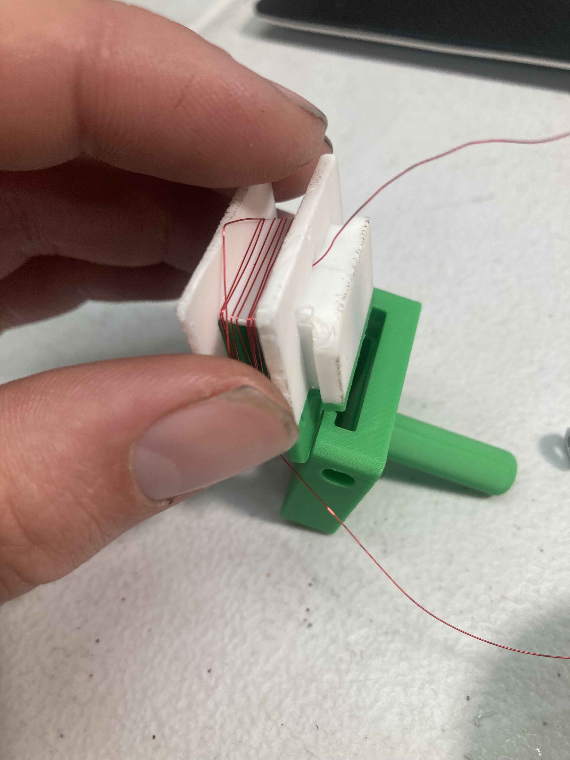
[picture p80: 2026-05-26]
Documentation/Workshop How To Zine V2/photos/Photos-3-001/IMG_7939.jpg

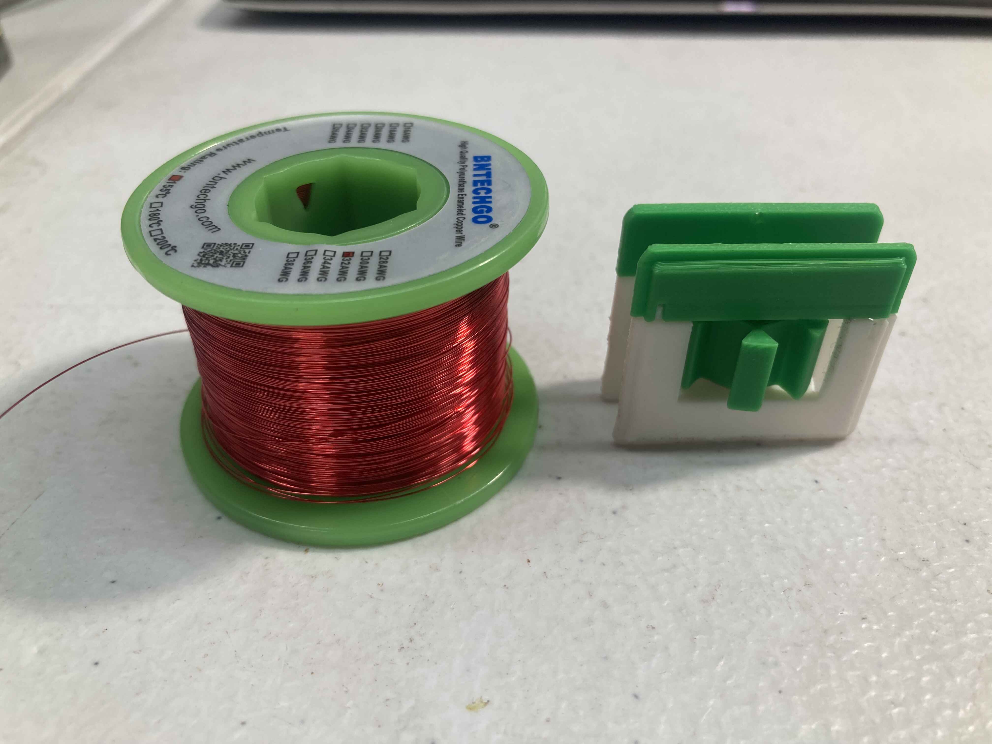
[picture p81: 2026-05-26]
Documentation/Workshop How To Zine V2/photos/Photos-3-001/IMG_7934.jpg

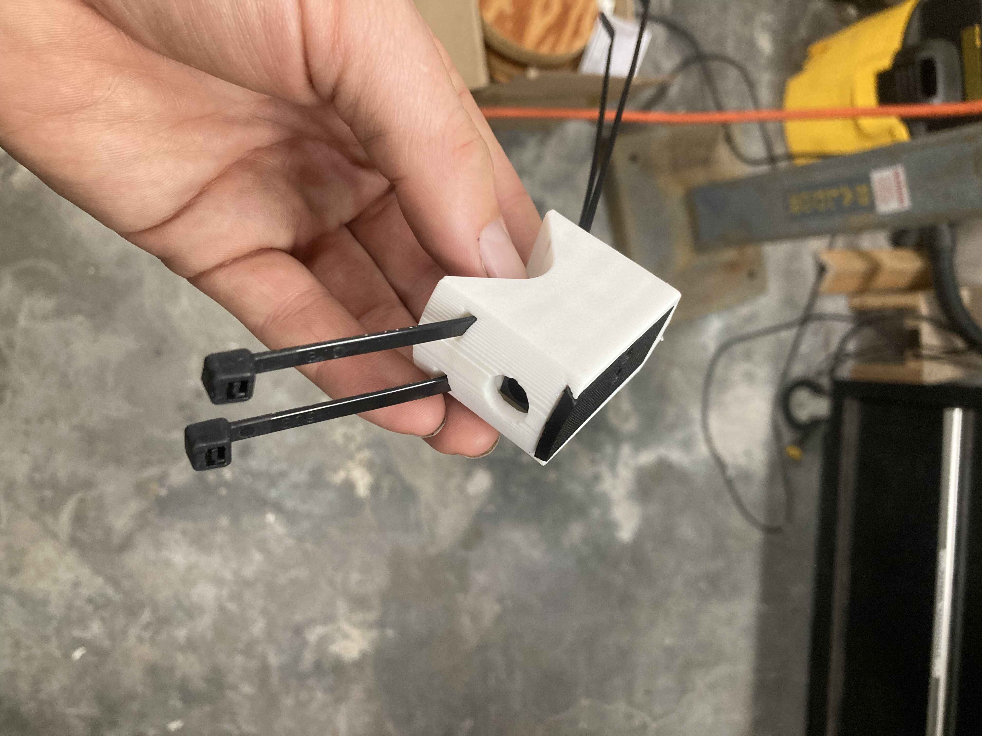
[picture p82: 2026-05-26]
Documentation/Workshop How To Zine V2/photos/Photos-3-001/IMG_7974.jpg

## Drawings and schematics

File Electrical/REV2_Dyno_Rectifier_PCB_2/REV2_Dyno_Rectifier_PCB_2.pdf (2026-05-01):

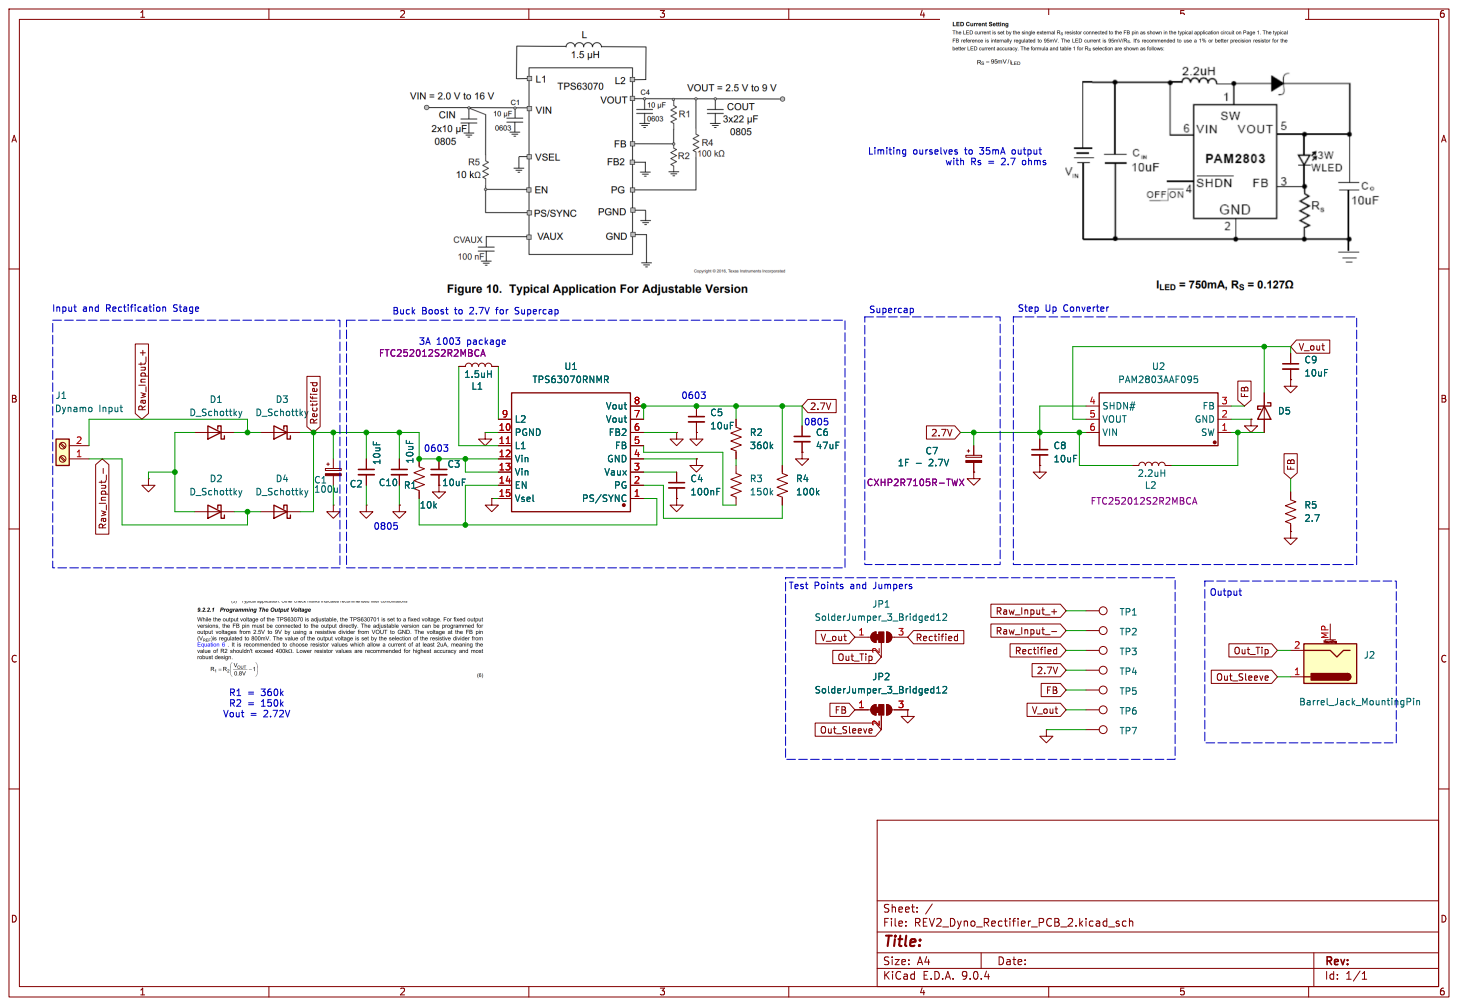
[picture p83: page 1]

Id: 1/1 Title: File: REV2_Dyno_Rectifier_PCB_2.kicad_sch Sheet: / 1

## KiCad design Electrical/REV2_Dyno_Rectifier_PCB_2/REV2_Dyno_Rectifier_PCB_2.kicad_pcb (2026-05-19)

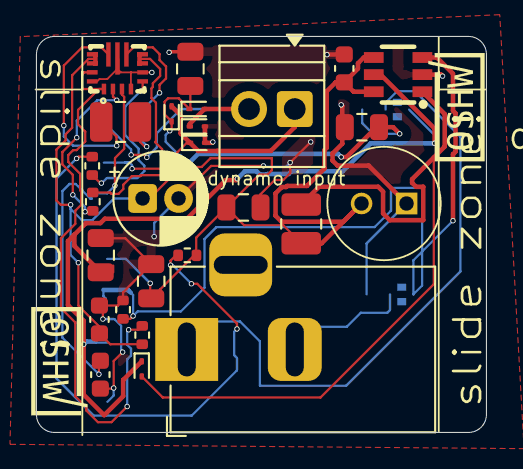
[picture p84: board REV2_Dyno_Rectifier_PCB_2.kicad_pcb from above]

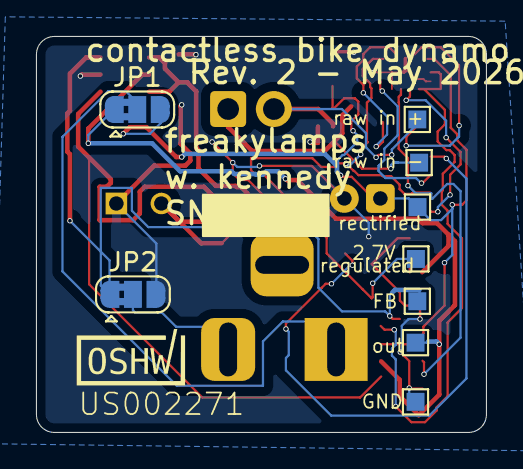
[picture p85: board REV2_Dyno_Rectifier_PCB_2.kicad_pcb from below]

Board: 2 copper layers, 25.0 x 22.0 mm, 35 parts (9 on the bottom side), 17 nets.

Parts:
C1: 100u; CP_Radial_D5.0mm_P2.00mm
C2, C8, C9, C10: 10uF; C_0805_2012Metric
C3, C5: 10uF; C_0603_1608Metric
C4: 100nF; C_0603_1608Metric
C6: 47uF; C_0805_2012Metric
C7: 1F - 2.7V; supercapacitor - 4mm diameter
D1, D2, D3, D4, D5: D_Schottky; D_SOD-923
J1: Dynamo Input; TerminalBlock_Xinya_XY308-2.54-2P_1x02_P2.54mm_Horizontal
J2: Barrel_Jack_MountingPin; BarrelJack_Horizontal
JP1, JP2: SolderJumper_3_Bridged12; SolderJumper-3_P1.3mm_Bridged2Bar12_RoundedPad1.0x1.5mm
L1: 1.5uH; L_1008_2520Metric
L2: 2.2uH; L_1008_2520Metric
R1: 10k; R_0402_1005Metric
R2: 360k; R_0402_1005Metric
R3: 150k; R_0402_1005Metric
R4: 100k; R_0402_1005Metric
R5: 1.8; R_0402_1005Metric
TP1, TP2, TP3, TP4, TP5, TP6, TP7: TestPoint; TestPoint_Pad_1.0x1.0mm
U1: TPS63070RNMR; TPS63070RNMR-2
U2: PAM2803AAF095; PAM2803_SOT-23-6_L2.9-W1.6-P0.95-LS2.8-BR

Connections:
2.7V: C5.1, C6.1, C7.1, C8.1, L2.1, R2.1, R4.1, TP4.1, U1.7 (Vout), U2.4 (SHDN#), U2.6 (VIN)
FB: JP2.1 (A), R5.1, TP5.1, U2.3 (FB)
GND: C1.2, C2.2, C3.2, C4.2, C5.2, C6.2, C7.2, C8.2, C9.2, C10.2, D1.2 (A), D2.2 (A), JP2.3 (B), R5.2, TP7.1, U1.4 (GND), U1.6 (FB2), U1.10 (PGND), U1.15 (Vsel), U2.2 (GND)
unnamed: D5.2 (A), L2.2, U2.1 (SW)
unnamed: R2.2, R3.1
unnamed: R1.2, U1.1 (PS/SYNC), U1.14 (EN)
unnamed: R3.2, U1.5 (FB)
unnamed: L1.1, U1.11 (L1)
unnamed: L1.2, U1.9 (L2)
unnamed: R4.2, U1.2 (PG)
unnamed: C4.1, U1.3 (Vaux)
Out_Sleeve: J2.2, JP2.2 (C)
Out_Tip: J2.1, JP1.2 (C)
Raw_Input_+: D1.1 (K), D3.2 (A), J1.2, TP1.1
Raw_Input_-: D2.1 (K), D4.2 (A), J1.1, TP2.1
Rectified: C1.1, C2.1, C3.1, C10.1, D3.1 (K), D4.1 (K), JP1.3 (B), R1.1, TP3.1, U1.12 (Vin)
V_out: C9.1, D5.1 (K), JP1.1 (A), TP6.1, U2.5 (VOUT)

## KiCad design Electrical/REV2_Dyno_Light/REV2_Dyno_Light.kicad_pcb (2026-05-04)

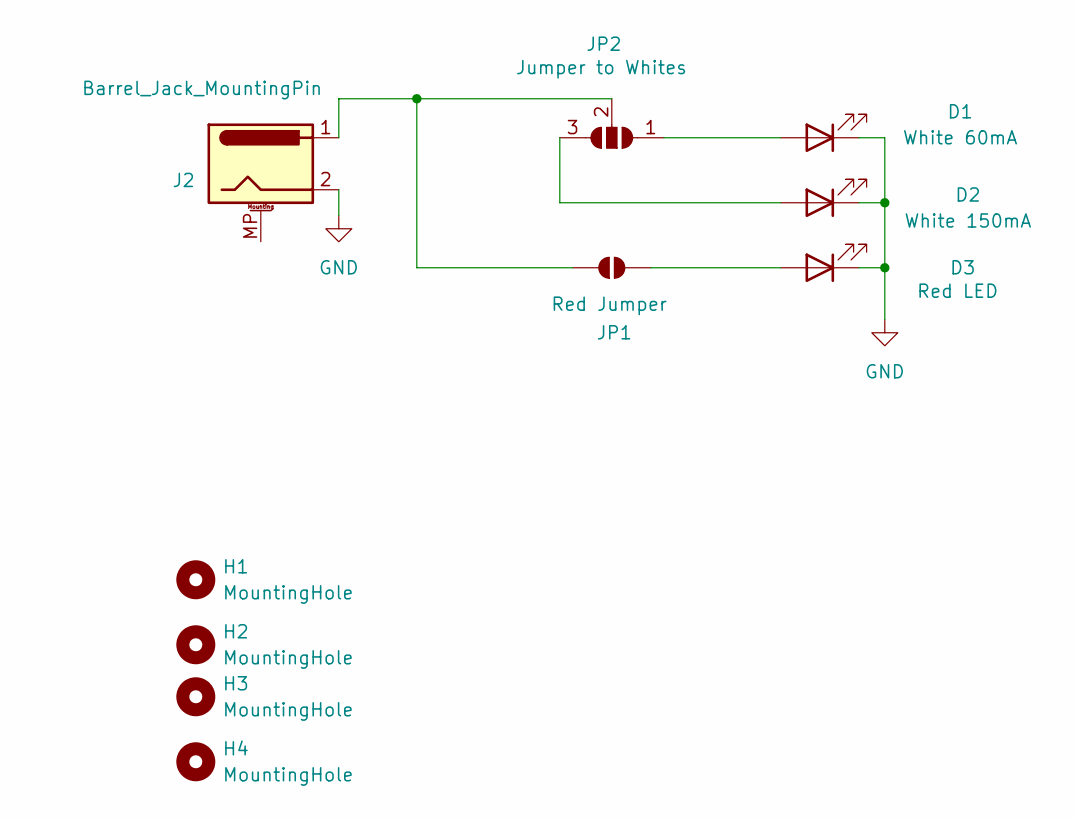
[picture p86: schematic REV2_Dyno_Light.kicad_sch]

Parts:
D1: White 60mA; LED_PLCC_2835; LCSC C210310
D2: White 150mA; LED_PLCC_2835; LCSC C210320
D3: Red LED; LED_PLCC_2835
H1, H2, H3, H4: MountingHole; MountingHole_3.2mm_M3
J2: Barrel_Jack_MountingPin; BarrelJack_Horizontal; LCSC C16214
JP1: Red Jumper; SolderJumper-2_P1.3mm_Open_TrianglePad1.0x1.5mm
JP2: Jumper to Whites; SolderJumper-3_P2.0mm_Open_TrianglePad1.0x1.5mm_NumberLabels

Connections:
GND: D1.1 (K), D2.1 (K), D3.1 (K), J2.2
unnamed: D1.2 (A), JP2.1 (A)
unnamed: D2.2 (A), JP2.3 (B)
unnamed: D3.2 (A), JP1.2 (B)
unnamed: J2.1, JP1.1 (A), JP2.2 (C)

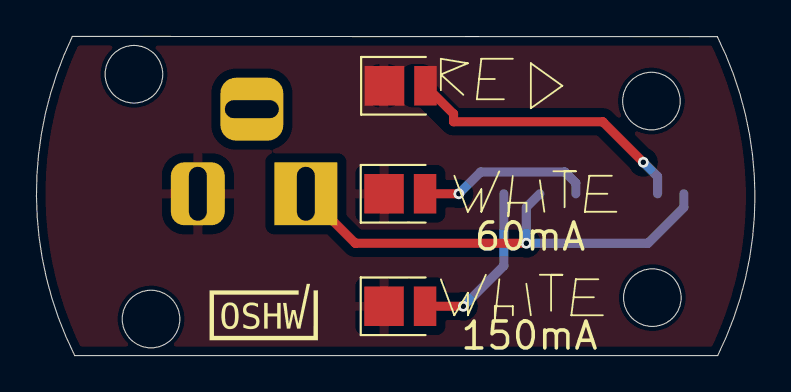
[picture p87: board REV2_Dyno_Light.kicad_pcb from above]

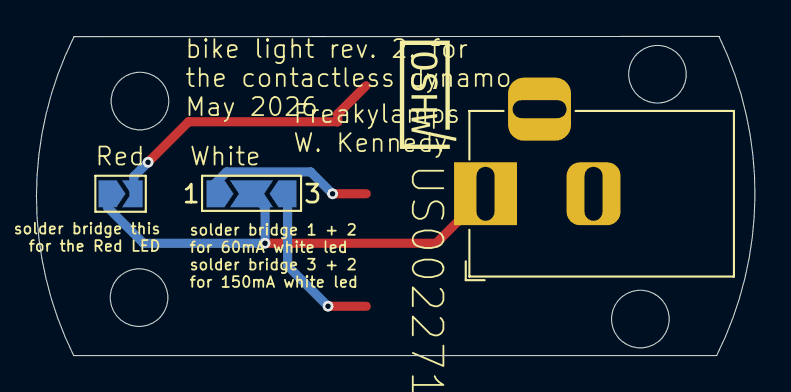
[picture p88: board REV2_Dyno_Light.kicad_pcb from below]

Board: 2 copper layers, 39.9 x 17.7 mm, 10 parts (3 on the bottom side), 5 nets.

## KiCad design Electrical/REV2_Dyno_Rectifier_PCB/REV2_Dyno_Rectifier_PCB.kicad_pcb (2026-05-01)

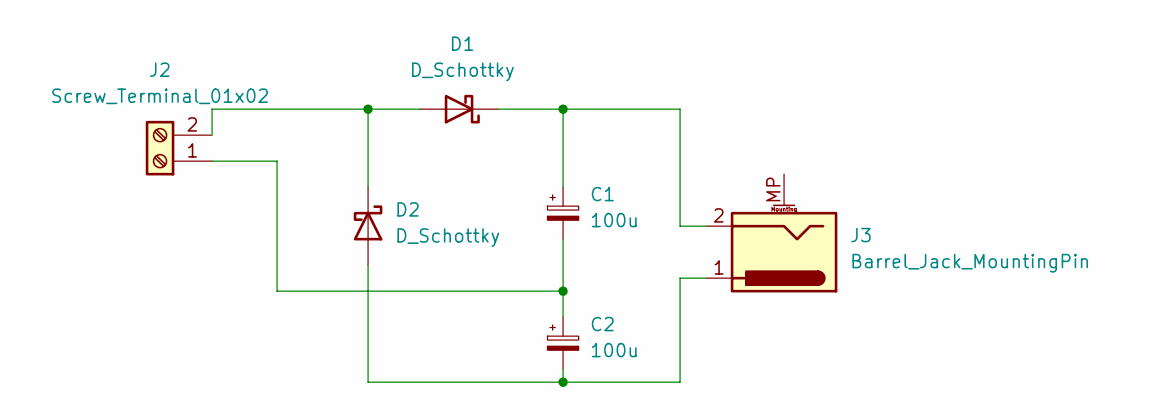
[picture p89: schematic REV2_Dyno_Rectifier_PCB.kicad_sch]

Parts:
C1, C2: 100u; CP_Elec_6.3x7.7; LCSC C3338
D1, D2: D_Schottky; D_SOD-123; LCSC C8570
J2: Screw_Terminal_01x02; TerminalBlock_Xinya_XY308-2.54-2P_1x02_P2.54mm_Horizontal; LCSC C557685
J3: Barrel_Jack_MountingPin; BarrelJack_Horizontal; LCSC C16214

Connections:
unnamed: D1.2 (A), D2.1 (K), J2.2
unnamed: C1.1, D1.1 (K), J3.2
unnamed: C2.2, D2.2 (A), J3.1
unnamed: C1.2, C2.1, J2.1

Board: 2 copper layers, 6 parts (0 on the bottom side), 4 nets, no tracks yet.

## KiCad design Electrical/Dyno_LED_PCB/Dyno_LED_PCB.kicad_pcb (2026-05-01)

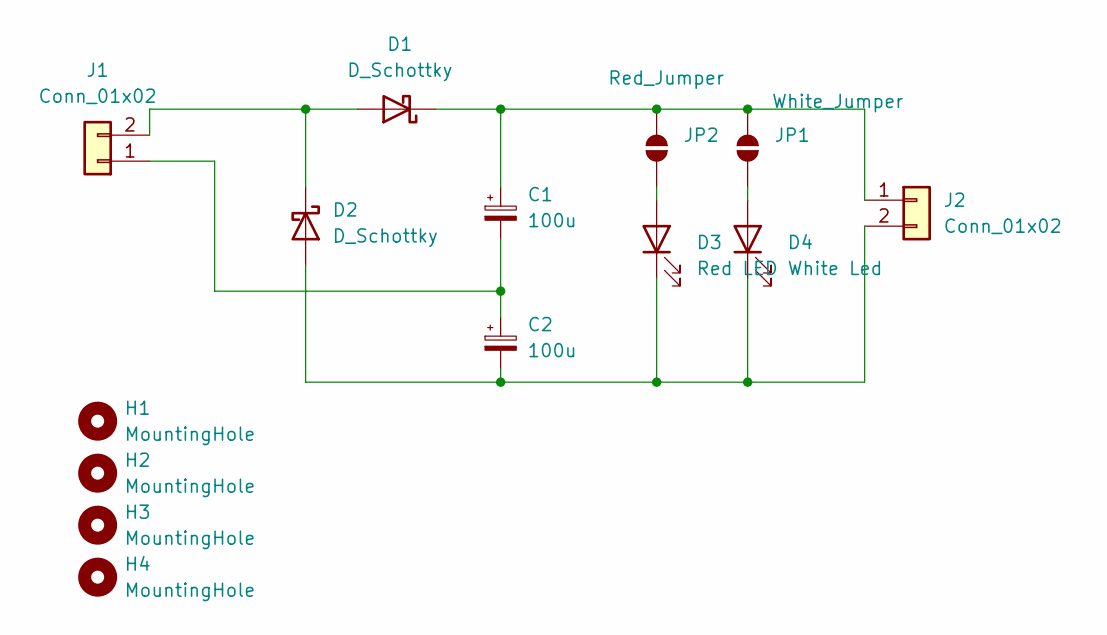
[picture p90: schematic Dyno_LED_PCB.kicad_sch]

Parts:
C1, C2: 100u; CP_Elec_6.3x7.7
D1, D2: D_Schottky; D_SOD-123
D3: Red LED; LED_1206_3216Metric
D4: White Led; LED_1206_3216Metric
H1, H2, H3, H4: MountingHole; MountingHole_2.2mm_M2
J1: Conn_01x02; JST_XH_B2B-XH-A_1x02_P2.50mm_Vertical
J2: Conn_01x02; PinHeader_1x02_P2.54mm_Vertical
JP1: White_Jumper; SolderJumper-2_P1.3mm_Open_RoundedPad1.0x1.5mm
JP2: Red_Jumper; SolderJumper-2_P1.3mm_Open_RoundedPad1.0x1.5mm

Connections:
unnamed: D1.2 (A), D2.1 (K), J1.2
unnamed: C1.1, D1.1 (K), J2.1, JP1.2 (B), JP2.2 (B)
unnamed: C2.2, D2.2 (A), D3.1 (K), D4.1 (K), J2.2
unnamed: D3.2 (A), JP2.1 (A)
unnamed: D4.2 (A), JP1.1 (A)
unnamed: C1.2, C2.1, J1.1

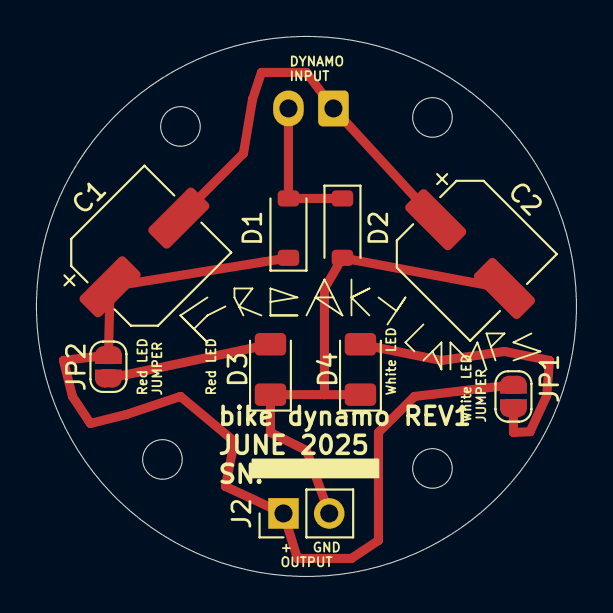
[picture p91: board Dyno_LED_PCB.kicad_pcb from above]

Board: 2 copper layers, 30.0 x 30.0 mm, 14 parts (1 on the bottom side), 6 nets.

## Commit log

2025-08-13 adding readme, more documentation
    [bike Dynamo.blend]
2025-08-13 adding bill of materials, updating readme
2025-08-13 made BOM into CSV files instead of a google sheet
    [Bill of Materials - Parts_REV1 .csv, Bill of Materials - Tools Needed_REV1.csv]
2026-04-14 starting to work on V2 design files
    [Dynamo_Rev2A.SLDASM, Dynamo_Rev2C.SLDASM, P001-B100H_SquareDynamo.SLDPRT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]
2026-05-01 rev 2 circuit basically done, board almost laid out, also mechanical updates
    [92000A343_Passivated 18-8 Stainless Steel Pan Head Phillips Screws.SLDPRT, 9262K142_Oil-Resistant Buna-N O-Ring.SLDPRT, 94300A320_Zinc-Plated Steel Wing Nut.SL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]
2026-05-01 schematic should be done! component placement almost done
    [BOM-REV2_Dyno_Rectifier_PCB.csv, BOM-REV2_Dyno_Rectifier_PCB_2.csv, Dynamo Assembly_2D-1.SLDASM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]
2026-05-04 sent off rectifier PCB and the Light PCB off to JLCPCB tonight
    [BOM-REV2_Dyno_Light.csv, BOM-REV2_Dyno_Rectifier_PCB_2.csv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]
2026-05-19 V2 is (pretty much) done! need to organize things better but it is all here!
    [8x3x4 Ball Bearing.SLDPRT, Bobbin_top + winding plate attachments x 25.3mf, FrontCoverx26.3mf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]
2026-05-26 cleaning up documentation a little bit
    [Bill of Materials - Parts_REV1 .csv, Bill of Materials - Tools Needed_REV1.csv, P001 - D006 - Bill of Materials.xlsx]
